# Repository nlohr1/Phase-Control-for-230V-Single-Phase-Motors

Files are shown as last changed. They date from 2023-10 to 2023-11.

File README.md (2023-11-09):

### Readme-Content:
- [Basic Schematic](#phase-control-for-230v-single-phase-motors-v2)
- [Module-Alignments](#alignment-v2-of-used-modules-on-a-5mm-acrylic-base-board)
- [Main-Schematic](#main-schematic--wiring-connections)
- [Safety-features](#safety-features)
- [Disclaimer](#readme-contents)
- [Principle-description](#principle-description)
- [The Wiring Board](#the-wiring-board)
- [Speedometer](#speedometer)
- [Schematic and Layout of the DIY-Speedometer](#diy-speedometer)
- [DIY-Boards + PCB-Layout](#diy-boards)

# Phase-Control-for-230V-Single-Phase-Motors
### Corrections and small modifications on new version Main_v2:  
- Another alignment purpose, which saves space.  
- The Emergency-Switch now is placed correctly within the "Off"-Switch wiring-line. Previoulsy it was wrongly placed within "On"-Switch line.  
- A second, passive 220k&Omega;2W-Resistor is placed after the Reversing-Switch between the two Motor-Supply-Lines (U1 and U2), instead on the wiring-board, to ensure save voltage-unload of the Motor-"Fire" EMI-Filter.

**⇒ &nbsp;New files in v2:**  
&#45; Main_v2 (base-folder for v2)  
&#45; Wiring-Board-Nano_v2 (sub-folder)  

This is a Control-Board for direction-switchable 230V *direct current* (DC)-motors, whose speed (rpm) can be controlled using a Potentiometer *or*  
using a PWM (Pulse Width Modulation) Signal in the low voltage range, generated here by a microController (Arduino Nano).

&nbsp; &nbsp;*Phase-Control schematic: **Priciple for 230V DC-Motors** with reversing-switch.*  
325V-DC-Motor-on-Phase-Control_Principle-Diagram

The picture above shows a basic diagram for the electronic control of a 230V **DC** motor, e.g. a hobby lathe, connected to a **single-phase** (230V) **AC**-current network.

Phase control circuits are often used for simple speed controls, here with an additional Bridge-Rectifier for 230V DC electric motors,
which are often used in medium power hobby machines (up to 10 amps ≙ approx. 2300 watts), such as lathes, milling benches, etc.

### Alignment-v2 of used modules on a 5mm acrylic base-board:
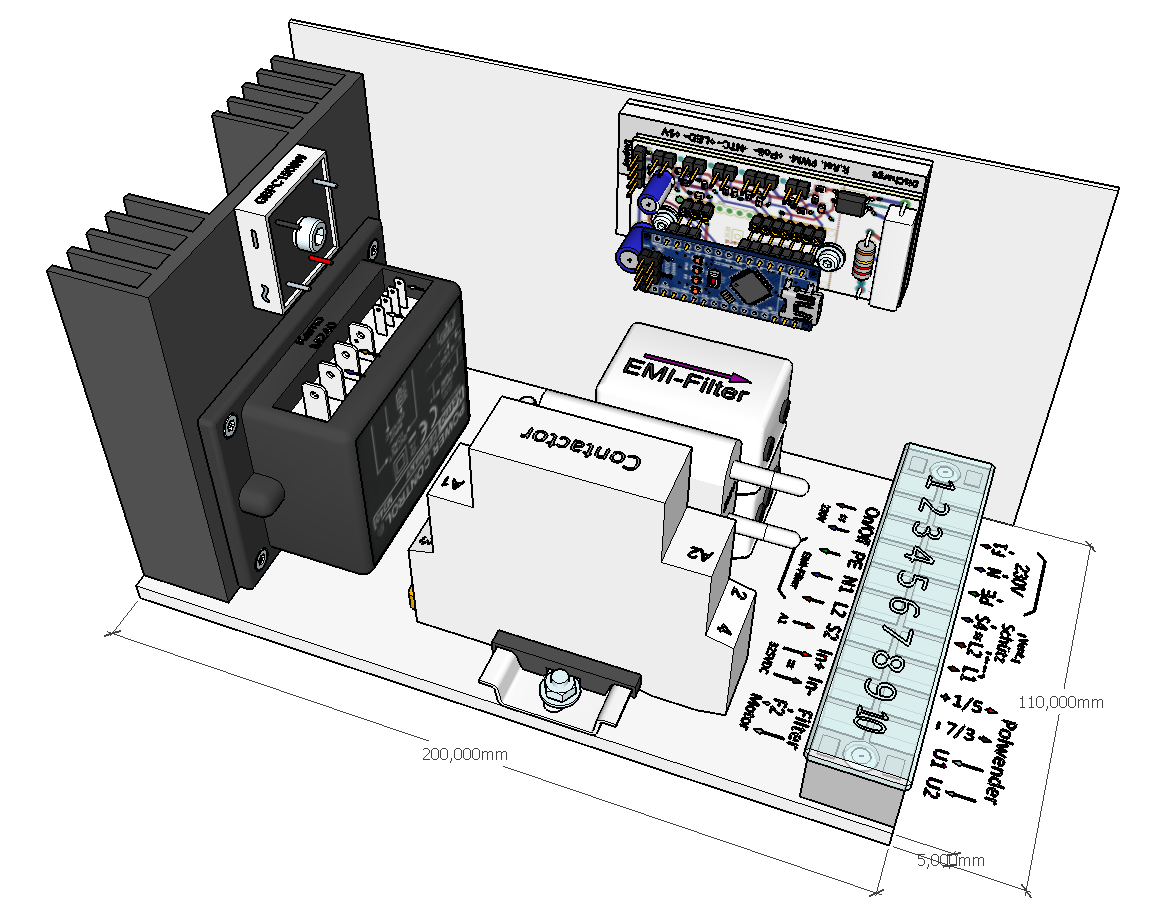
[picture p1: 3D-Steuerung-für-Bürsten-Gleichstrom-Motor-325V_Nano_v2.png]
3D-Steuerung-für-Bürsten-Gleichstrom-Motor-325V_Nano_v2
  
Since electronic controls of 230V *DC* motors in today's hobby machines (such as lathes, milling benches, etc.) often are built with
inexpensive components that are not really protected against surges or current peaks – some electronic-failures are inevitable.
So I decided to use a circuit that works a little more reliable, with electronic components and *modules* that are readily available
on the market *and* at the same time are better protected against voltage-glitches, overloads, incorrect operations and engine over-temperature.
All 230VDC (Direct Current!) brushed motors with up-to 2300 Watts can be controlled with this phase control board. It allows to control
the speed of the motor (0-100%) as well as the motor direction of rotation.

### Main Schematic / Wiring Connections:
⇒ *(the DIY-Wiring-Board with the Ardujino-nano here is yellow-framed)*
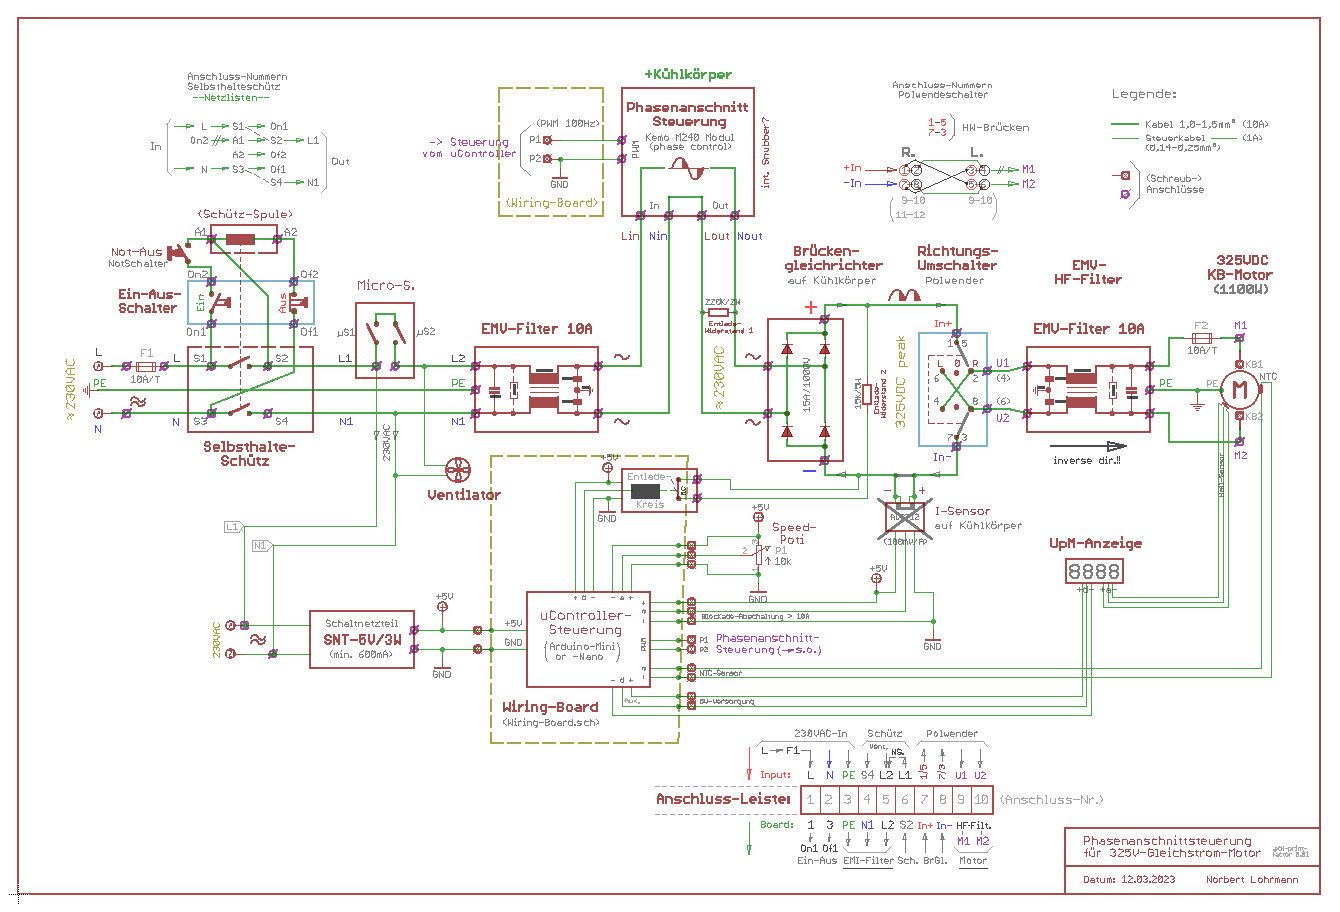
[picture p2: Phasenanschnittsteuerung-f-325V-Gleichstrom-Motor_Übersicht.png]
Phasenanschnittsteuerung-f-325V-Gleichstrom-Motor_Übersicht_DE


## Safety features
This circuit has some essential safety-functions:
- The main module "Kemo-M240" used here contains an integrated soft start, needed to start up strong motors (>800 - 2300 Watts),
   to avoid the tripping of standard 16A household fuses
- This main-module also contains an automatic overload or anti-lock shutdown with electronic reset
- If the used Motor contains a built-in NTC-thermistor (with 100kOhm), the µController can provide a protection against
   engine overheatings: if the motor-temperature exceeds 80°C, the µC goes into an endless loop, and reactivating PWM
   is only possible by switching off (main-power) or by pushing the reset-button of the µC.

!!!: Protection against direction of rotation switching ***while driving*** is **NOT** provided: if so an "EMF short circuit" occurs,
the "Kemo-M240" controller shots the power-control off in a fractions of a second and thus at least the mechanics of the machine is protected.
Electronics then can only be reactivated after a complete restart - either per µContoller-Reset or after a complete Main-Power Shutdown.

## Disclaimer:  
!!! It goes without saying that you reproduce this circuit at your own risk and responsibility !!!
Anyone who does not have sufficient knowledge of how to handle *dangerous* 230VAC currents or 325VDC(ss) voltages(!):
If you are not familiar with electrical or electronic components, you should either hire a specialist to do it for you
or stay away from it!
“Experiments” without special knowledge and appropriate protection(s) on high voltages can quickly end in death
following an electric shock! And sudden cardiac-arrest can occur even days after an electric shock! - if then
no immediate help is nearby...
In any case, a replica of this project is done expressly and explicitly *at your own risk*!

**Further notes:**
- Three-phase motor control is excluded due to the principle! This circuit only controls single phase Engines!
- The circuit also works with (simpler) *AC* single-phase asynchronous motors - omitting the bridge rectifier used here.
   However, a connected ***AC*** motor then is no longer direction-reversible.
- It is NOT suitable for capacitor motors! - "Capacitor starting motors" are often only used for simple purposes and
   built+used for on/off operation only (such as for smaller hobby drill press machines) - and are not speed-regulated.
   But it depends specifically on the type of engine, some capacitor motors can still be regulated (speed-limited).
   However, any weak to poor efficiency that so occurs should be taken into account (including heat losses).

Factual suggestions for improvements and changes are always welcome!

## Principle description:
The control works according to the 230VAC phase control principle (similar to a lamp dimmer), but in contrast to this
it can neutralize EMF (electromotive forces) of greater motors and is determined by special selection of used electronic components.

The Kemo-240 control-module is controlled via PWM (Pulse Width Modulation). This (low-voltage: 5VDC) PWM-signal is generated
with a “Arduino-Nano” micro-controller and (if present), this µC also evaluates an NTC-Sensor installed within the Motor, to check
a possible motor-overtemperature.
The Speedometer (RPM display on a LED display) does not run - as usually *independently* of the main phase-control, 
but sends back a "busy" signal to the µController, which therefore "knows" when the motor is running or not
(=when it is standing still), in order to ensure active discharge of the triac snubber and the EMI or EMC-filters charged
through supplied voltages + motor back EMF, to avoid uncontrolled jerky startings of the DC-motor after changing the direction of rotation.

The control consists of several modules chained(wired) one behind the other:

1. the 10AT fuse (F1) and the on/off switch with the self-holding latching contactor,
2. the (mandatory) safety switches plus other 230V safety microswitches on the specific machine,
3. the upstream EMC filter (= ElectroMagnetic Compatibility), here called EMI filter (serves to avoid incoming E.M. interferences),
4. the actual (triac) phase control, using *either* a potentiometer *or* a µController with PWM-output (Pulse-Width Modulation),
5. in parallel the 5V low-voltage circuit with the "Arduino-Nano" module, to generate the PWM for the phase control (2nd. version), 
   with additional, software-side monitoring of eventual motor-over-temperature,
6. the 15A/1500V bridge rectifier,
7. the reversing switch, also called “pole inverter” or direction of rotation switch,
8. a second EMI (carbon-brush-"fire"-) suppression filter + a second 10AT motor fuse (F2), and
9. at last the 325V DC (=direct current) motor.

230v-Wiring between modules and the outside-parts (rear 230V inlet-panel, front machine-control-panel, motor-connections) have to be connected safely
through PVC-isolated 1mm² wires (about AWG 17) and in-between through isolated threaded-connectors or clamping-connectors with 16A/230V.
I used lever clamps ("WAGO Hebelklemme 221-2411") for most of the "flying"-connections.  
For all 5Volt (=low-voltage) connections I used smaller wires (about 0.25-0.75mm² = AWG-23 upto AWG-20) with JST-Connectors (2-, 3- and 4-wired),
as connectors for the wiring-board. Of course also it's possible to use above mentionned WAGO-connectors for smaller wires.  
**Att: Reliability of connections** is VERY IMPORTANT, so dont choose cheap (=mostly bad) connectors, due to 99% of all electical problems
are resulting from loose contacts/connections!

## The Wiring Board:
The two DIY-parts in this chain that still needs to be soldered together + programmed are the “wiring board” and the DIY-Speedometer.  
The Wiring-board serves to wire/connect the Low-Voltage PWM-Signal to the main phase control module "Kemo-M240" and to other low-voltage connections
as the Panel-Signal-"On"-LED, the NTC-Sensor and the 10k&Omega;-Poti.  
This wiring board also contains the Arduino Nano µController as the heart of the circuit, some passive components (resistors + capacitors) and above mentionned
(JST-)Connectors plus a 4-wire JST-Connector for the Speedometer (rpm display) and the 230VAC Discharge Circuit (Power-Resistor), this to avoid uncontrolled,
jerk startings of the motor while switching it into reverse-direction.
Wiring-Board-Nano_sch
*Circuit diagram of the low-voltage circuit "wiring board" with the Arduino Nano*  
Wiring-Board-Nano_3D

This wiring board with the Arduino Nano is provided as schematic and as PCB-layout in Eagle format - which can easily be converted
into other formats. Included are also .pdf-files and layouts, prepared for the DIY "toner-direct-method" and for external PCB-Services.

## Speedometer:
Speedometer

## DIY-Speedometer:
4x7-Segment-LED-Display-Module

**Schematic and Layout of the DIY-Speedometer**:  
Tachometer-with-4x7-Segm-LED-Display_sch
Tachometer-with-4x7-Segm-LED-Display_pcb

The DIY-Speedometer consists of a 4-digit LED-display-module and a "Arduino Mini Pro"-module (inside the case) with 2 pieces of 10k resistors to GND.  
This tachometer can either be “manually wired”:
- by wire-connecting a 4-digit LED-Display module to a (Arduino-)Mini-Pro board + 2x 10k resistors to GND,
   or
- soldering SMD-parts on a DIY-Board with above provided layout. For this purpose I included Schematic + Layout, as well as BOM (Bill of Materials).

A speedometer to display the speed of the motor can also be purchased as a (ready-made) module - but this modules have no "running" monitor Signal and
so the discharge-unit (on the wiring-board) is no longer switching on/off (as needed for the 15k-Resistor R9).

## DIY-Boards:
Anyone who is familiar with DIY-etching of circuit boards can either use the 2-sided Toner Direct Method (see .pdf plans for 2-sided copy in 1:1 scale) or
give-it-out to an external PCB layout-service.  
In a further -separate- article I will describe a new and simpler method to make exact 2-sided DIY-PCB-layouts through laser-burning "resting"
ink-protect areas on the PCB-board (resting "black" areas: substracted isolated wiring-lines from the total surface).

All Documents are available as Eagle layouts, png-Image-Files and pdf-Files and also as Gerber+Excellon files (attached CAM .zip archives).  
So also both Arduino Sketches (for the Arduino-Nano "heart"-Module: "Firmware-Nano.ino" and the Sketch for the **DIY**-Speedometer-*Board* including a "naked"
ATmega328-µController + 4x7-LED-Display ***or*** for the wired version with an Ardino-Mini-Pro-*Module* + 4x7-LED-Display(-module).  
Both variants of the DIY-Speedometer are using the "Tachometer-using-Arduino.ino" sketch.  

Thereto I've enclosed also a 3D-printable case + frame-parts for the Tachometer, adapted to insert+glue the 4x7-LED-Display module.
-----

Github-Link: [https://github.com/nlohr1/Phase-Control-for-230V-Single-Phase-Motors](https://github.com/nlohr1/Phase-Control-for-230V-Single-Phase-Motors/blob/main/README.md)

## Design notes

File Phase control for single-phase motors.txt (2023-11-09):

Phase control for single-phase motors - up to 2300 watts
--------------------------------------------------------

Control for direction-switchable 230V *direct current* motors, whose speed (rpm) can be controlled using a
10k potentiometer *or* a PWM (pulse width modulation in the low voltage range) can be controlled via uController.

Priciple of a Poti-Controlled Phase-Control of 230AC/320VDC Motor
(3D image of the entire motor control)

Phase control circuits are often used for speed control, here a PA with a downstream one
Rectifier for reversible 230V DC electric motors, which are often used in hobby machines
medium power (up to 10 amps or up to approx. 2300 watts) such as lathes and milling benches.

Since the electronic controls of 230V *DC* motors in today's hobby machines such as lathes, milling benches, etc.
often have inexpensive components that are not protected against surges or current peaks – therefore
unfortunately failures are inevitable, so I decided to use a circuit that works a little more reliable,
with electronic components and *modules* that are readily available on the market and more reliable.
All 230VDC (direct current!) carbon brush motors with up to 2300W can be controlled with this phase control.
It allows you to control the speed of the motor (0-100%) as well as the motor direction of rotation.

Safety features of this single-phase speed-control:

In addition, this circuit has essential safety circuits:
- The main module "Kemo-M240" used here contains an integrated soft start, needed to start up larger motors,
   to avoid the tripping of standard 16A household fuses
- This module also contains an automatic overload or anti-lock shutdown with electronic reset
- If the motor contains a built-in NTC thermistor (with 100kOhm), the µController can provide a possible
   Monitor engine overheating protection. When 80°C is exceeded, the µC switches off the PWM goes into an endless loop,
   and can then only be reactivated by switching off the power or by pushing the reset-button of the controller.

!!!: Protection against direction of rotation switching *while driving* is NOT provided here: Due to this, if
an "EMF short circuit" occurs, the "Kemo-M240" controller switches off very quickly and thus at least protects
the mechanics of the machine. The electronics can then only be used again after a complete restart or Power shutdown.

Disclaimer:
!!! It goes without saying that you reproduce this circuit at your own risk and responsibility!!!
Anyone who does not have sufficient knowledge of how to handle *dangerous* 230VAC currents or 325VDC(ss) voltages(!):
If you are not familiar with electrical or electronic components, you should either hire a specialist to do it for you
or stay away from it!
“Experiments” without special knowledge and appropriate protection(s) on high voltages can quickly end in death
following an electric shock! And sudden cardiac-arrest can occur even days after an electric shock! - if then
no immediate help is nearby...
In any case, a replica of this project is done expressly and explicitly *at your own risk*!

Further notes:
- Three-phase motor activations are hereby excluded due to the principle! This circuit only controls single phase Engines!
- The circuit also works with (simpler) *AC* single-phase asynchronous motors - omitting the bridge rectifier used here.
   However, a connected *AC* motor then is no longer direction-reversible.
- It is NOT suitable for capacitor motors! - "Capacitor starting motors" are often only used for simple purposes and
   built + used for on/off operation only (such as for smaller hobby drill presses) - and are not speed-regulated. But
   it depends specifically on the type of engine, some capacitor motors can still be regulated (speed-limited).
   However, any weak to poor efficiency that occurs should be taken into account (including heat losses).

Factual suggestions for improvements and changes are always welcome!

(principle sketch)

The picture shows a possible, basic structure or the basic diagram of the electronic control
DC motor, e.g. a hobby lathe, which is connected to a single-phase 230VAC alternating current network - therefore
This circuit is only designed for a maximum output of 2300 watt motors (=> 10A fuse!) - but what
should be sufficient for most machines in the hobby sector (⇒ pay attention to the motor nameplate!).

(Main Wiring Diagram)

Principle description:
The control works according to the 230VAC phase control principle (similar to a lamp dimmer), but in contrast
it may neutralize the EMF (electromotive force) of a motor and is determined by the selection of electronic components.
A higher quality module is used to control the motor, which is controlled via PWM (Pulse Width Modulation).
The micro-controller “Arduino-Nano” used here generates the PWM and (if present) it also evaluates an NTC sensor
installed in the motor, to check any possible Engine overtemperature.
The speedometer for speed display does not run - as usually - *independently* of the main control (RPM display on a LED display), 
but also sends back a "busy" signal to the µController, which therefore "knows" when the motor is running or
when it is standing still, in order to ensure active discharge of the triac snubber and the EMI or EMC-filters charged
through supplied voltages and the motor back EMF, in order to avoid an uncontrolled, jerky starting of the DC-motor
after changing direction!

The control consists of several modules “wired” one behind the other:

1. the 10AT fuse and the on/off switch with latching contactor,
2. the (mandatory) safety switches or other 230V safety microswitches on a specific machine,
3. the upstream EMC filter (= electromagnetic compatibility), here called EMI filter (to avoid E.M. interferences),
4. the actual PWM (triac) phase control (control using a potentiometer *or* pulse-width modulation),
5. in parallel the low-voltage electronics (+5V/GND) to generate the PWM for the phase control, using an "Arduino-Nano"
    module with additional software-side monitoring of eventual motor-over-temperature with external NTC-sensor,
6. the 15A/1500V bridge rectifier,
7. the “pole inverter”, also called reversing switch or direction of rotation switch,
8. a second EMI (carbon brush fire) suppression filter + a second 10AT motor fuse,
9. and at last the 325V DC (=direct current) motor.

The only part that still needs to be soldered together + programmed is the “wiring board” to connect the Low-Voltage
PWM-Signal to the main phase control module "Kemo-M240". This wiring board contains also the Arduino Nano µController 
as the heart of the circuit, some passive components (resistors + capacitors) and the JST-Connectors for Sensors
and the tachometer (rpm display) + the Discharge Circuit for both Discharge Resistors, to avoid uncontrolled
starting impulses / jerk starting of the motor switching it to reverse-direction.

The “wiring board”:
(Circuit diagram of the low-voltage circuit "wiring board" with the Arduino Nano)
(3D image of the "wiring board")

The “wiring board” with the Arduino Nano is provided as schematic and as PCB-layout in Eagle format - which can
easily be converted into other formats.

Speedometer:
(Picture)

The modified speedometer consists of a 4-digit LED display and an "Arduino Mini Pro" with 2 pieces of
10k resistors to GND. This tachometer can either be “manually wired”:
- by wire-connecting the 4-digit LED-Display to the Mini-Pro + 2x 10k resistors to GND,
   or
- soldered together on a SMD-Board with the provided layout. Both Schematic + Layout as well as the BOM
  (Bill of Materials) + Software are included.

The speedometer for speed display/control can also be purchased as a (ready-made) module - but then
the running monitoring + also the unloading unit is no longer thereby (and can then be ignored).

Anyone who is familiar with the DIY production of circuit boards can either use the Toner Direct
Method (.pdf plans for 2-sided copy in 1:1 scale) or roll it out to an external PCB layout-service.
Documents are available both as Eagle layouts and as Gerber/Excellon files (in the .zip archive) attached.

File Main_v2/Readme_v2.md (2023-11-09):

### Readme_v2 Content:
- [Another Module-Alignment purpose]()
- [Main-Schematic v2]()
- [Wiring Board v2]()

# Phase-Control-for-230V-Single-Phase-Motors v2
### Corrections and small modifications on v2:  
- Another alignment purpose, which saves space  
- The Emergency-Switch now is placed within the "On"-Switch wiring-line. Previoulsy it was wrongly placed within "Off"-Switch line.  
- A second, passive 220k&Omega-Resistor is placed after the Reversing-Switch between the two Motor-Supply-Lines (U1 and U2), instead on the wiring-board, to ensure save voltage-unload of the Motor-"Fire" EMI-Filter.

**⇒ New files in in v2-folder:**  
&#45; this Readme_v2.md
&#45; Main_v2 (base-folder)
&#45; Wiring-Board-Nano_v2 (sub-folder)  

## Disclaimer:  
!!! It goes without saying that you reproduce this circuit at your own risk and responsibility !!!

### New Alignment of modules on the 5mm acrylic base-board in Base-board_v2:
![3D-Steuerung-für-Bürsten-Gleichstrom-Motor-325V_Nano_v2]()  

### Main Schematic_v2 / Wiring Connections:
⇒ *(the DIY-Wiring-Board with the Ardujino-nano here is yellow-framed)*
![Phasenanschnittsteuerung-f-325V-Gleichstrom-Motor_Übersicht_DE]()

## Wiring-Board_v2:
![Wiring-Board-Nano_v2]()
*Circuit diagram of the low-voltage circuit "wiring board" with the Arduino Nano*  
![Wiring-Board-Nano_3D_v2]()

<hr>

Github-Link: https://github.com/nlohr1/Phase-Control-for-230V-Single-Phase-Motors/

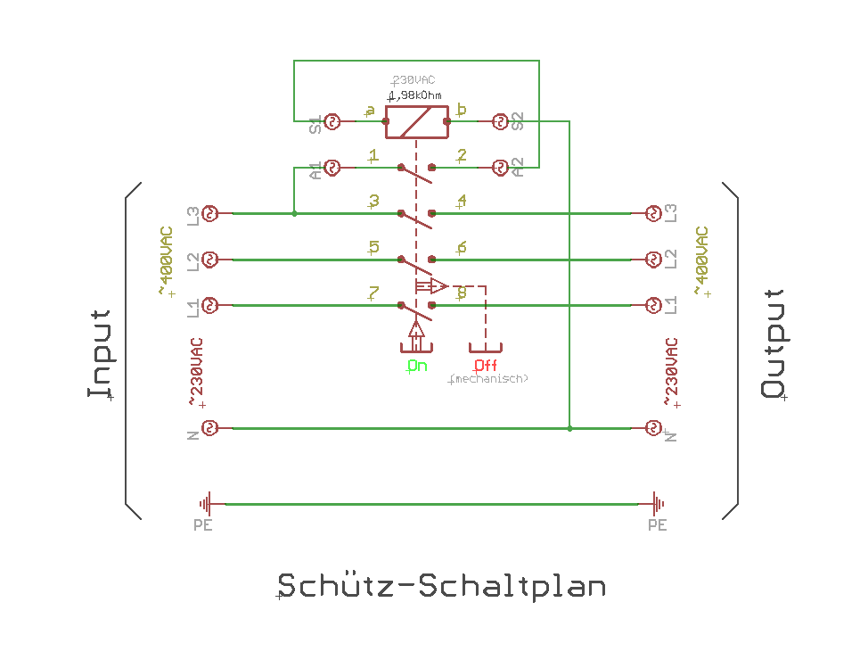
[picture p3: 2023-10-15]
DZ07B_EinAus-Schalter-mit-Schütz_Schaltplan-für-3-Phasen.png

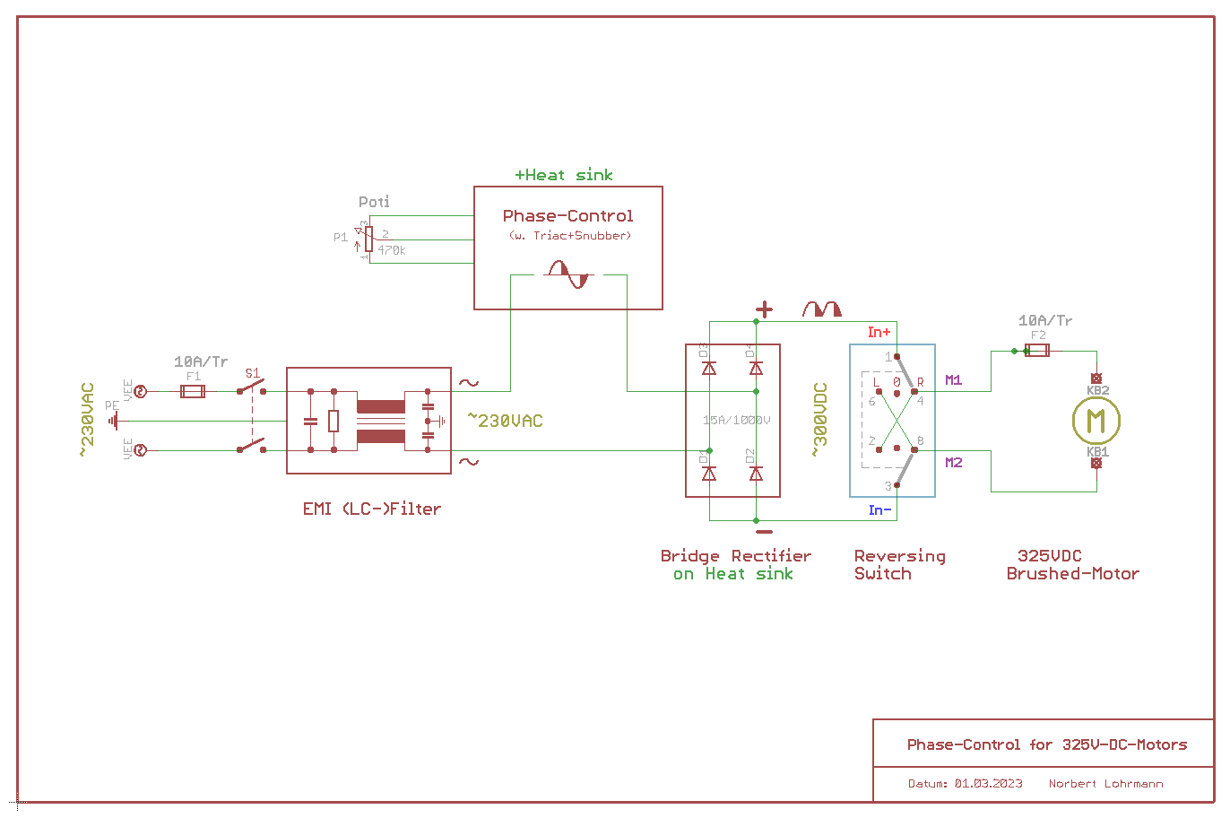
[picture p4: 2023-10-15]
325V-DC-Motor-on-Phase-Control_Principle-Diagram.png

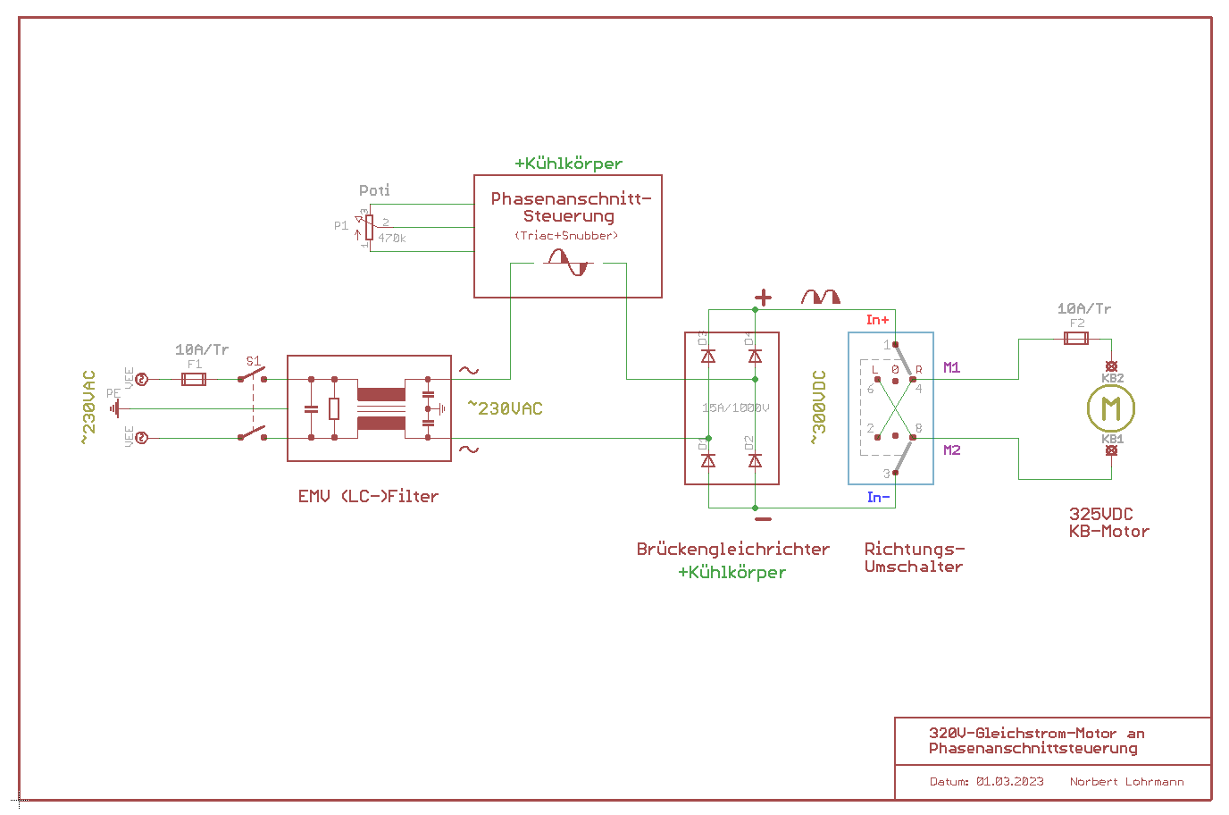
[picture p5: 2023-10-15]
325V-Gleichstrom-Motor-an-Phasenanschnittsteuerung_Prinzip-Schema.png

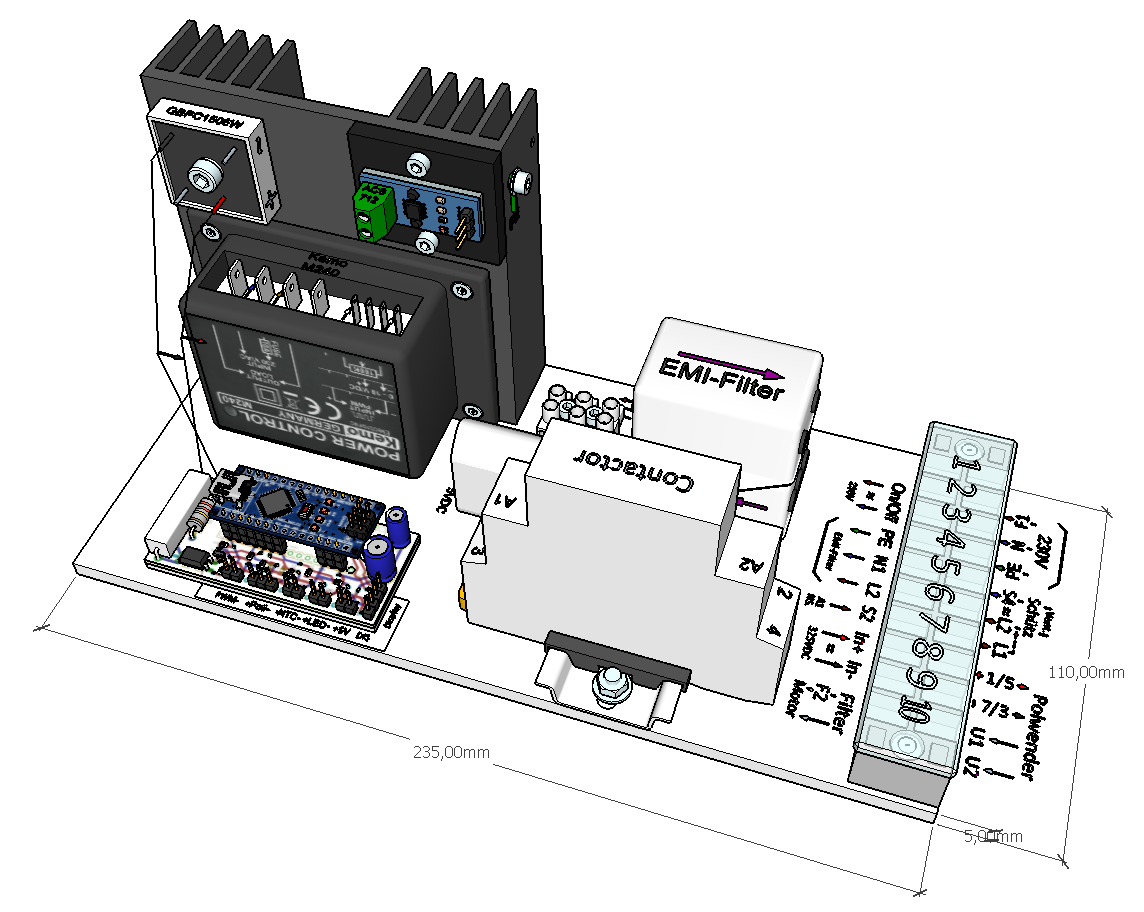
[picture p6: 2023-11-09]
3D-Steuerung-für-Bürsten-Gleichstrom-Motor-325V_Nano.png

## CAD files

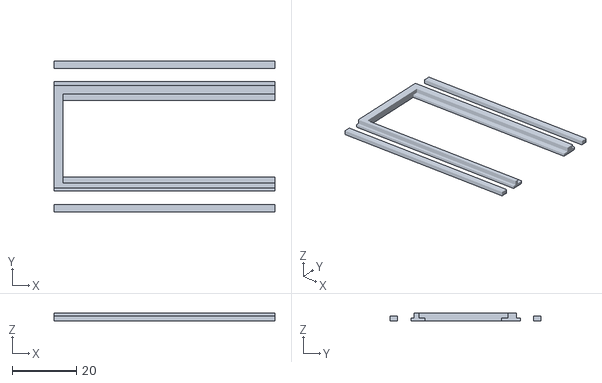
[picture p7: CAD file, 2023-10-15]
Tachometer_with_TM1637-IC_and_Arduino-Mini-Pro/Spacer-for-4x7-Segment-LED-Display-Frame.stl
69.0 x 47.2 x 2.50

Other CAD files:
Main_v2/Wiring-Board-Nano_v2/Wiring-Board-Nano_Bodenplatte.3mf
Main_v2/3D-Steuerung-f-Gleichstrom-Motor-325V_Lochung-der-Grundplatte_v2.skp
Main_v2/Wiring-Board-Nano_v2/Wiring-Board-Nano_3D_v2.skp
Main_v2/Wiring-Board-Nano_v2/Wiring-Board-Nano_Bodenplatte.stl
Tachometer_with_TM1637-IC_and_Arduino-Mini-Pro/4x7-Segment-LED-Display-Module.skp
Tachometer_with_TM1637-IC_and_Arduino-Mini-Pro/Spacer-for-4x7-Segment-LED-Display-Frame.skp
Wiring-Board-Nano/Wiring-Board-Nano_3D.skp

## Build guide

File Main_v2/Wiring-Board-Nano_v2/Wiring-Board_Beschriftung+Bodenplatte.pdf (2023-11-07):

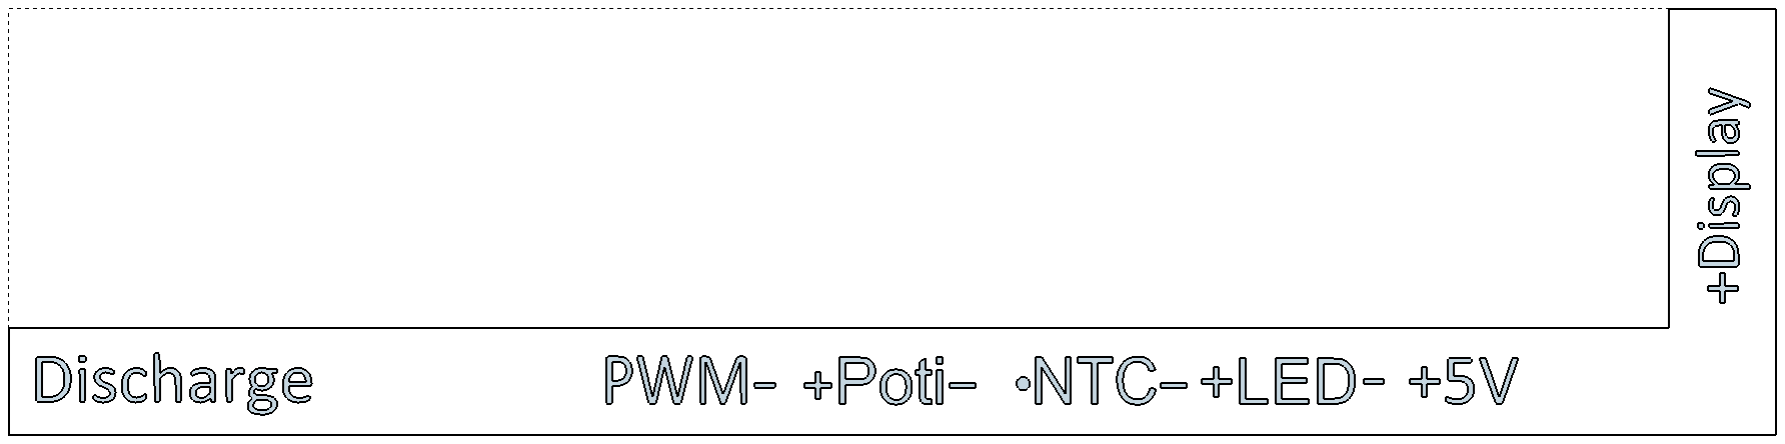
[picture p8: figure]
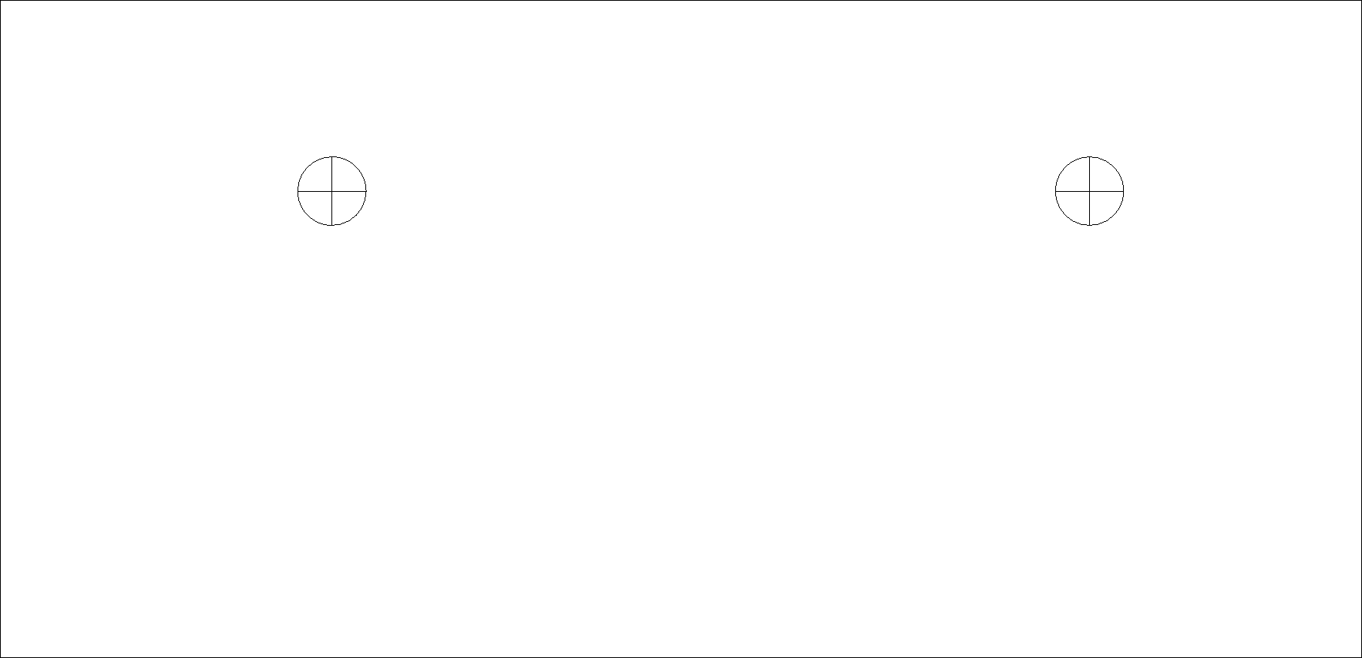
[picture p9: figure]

75,5 x 36,5 x #5 mm

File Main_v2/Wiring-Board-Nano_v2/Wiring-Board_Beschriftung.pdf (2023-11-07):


74,5 x 18 mm

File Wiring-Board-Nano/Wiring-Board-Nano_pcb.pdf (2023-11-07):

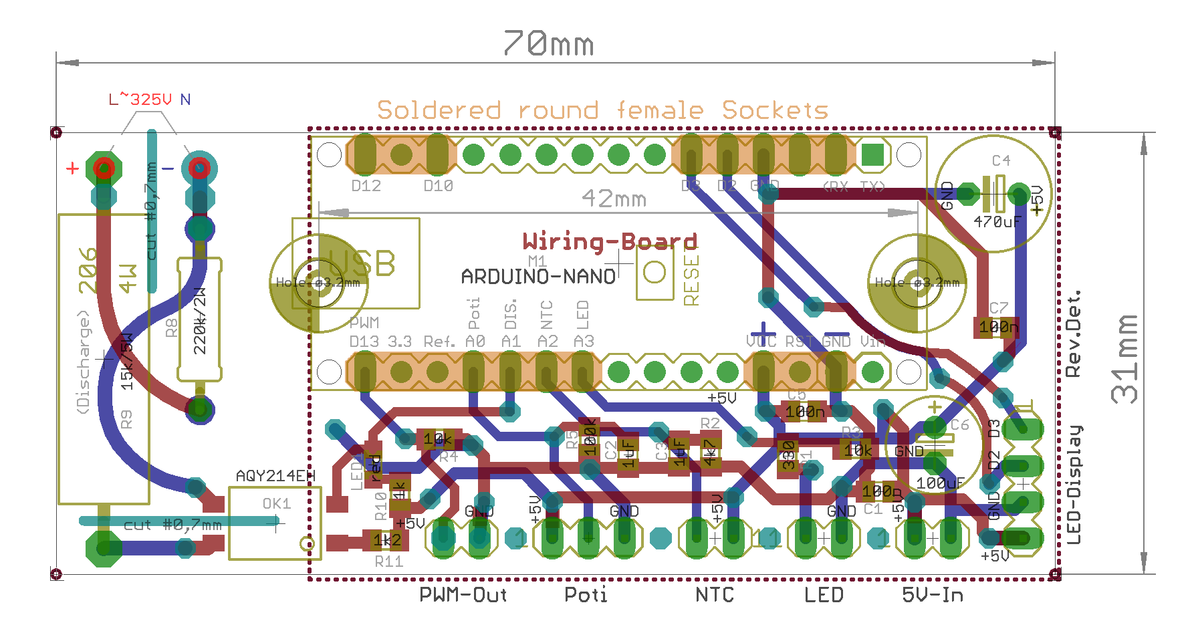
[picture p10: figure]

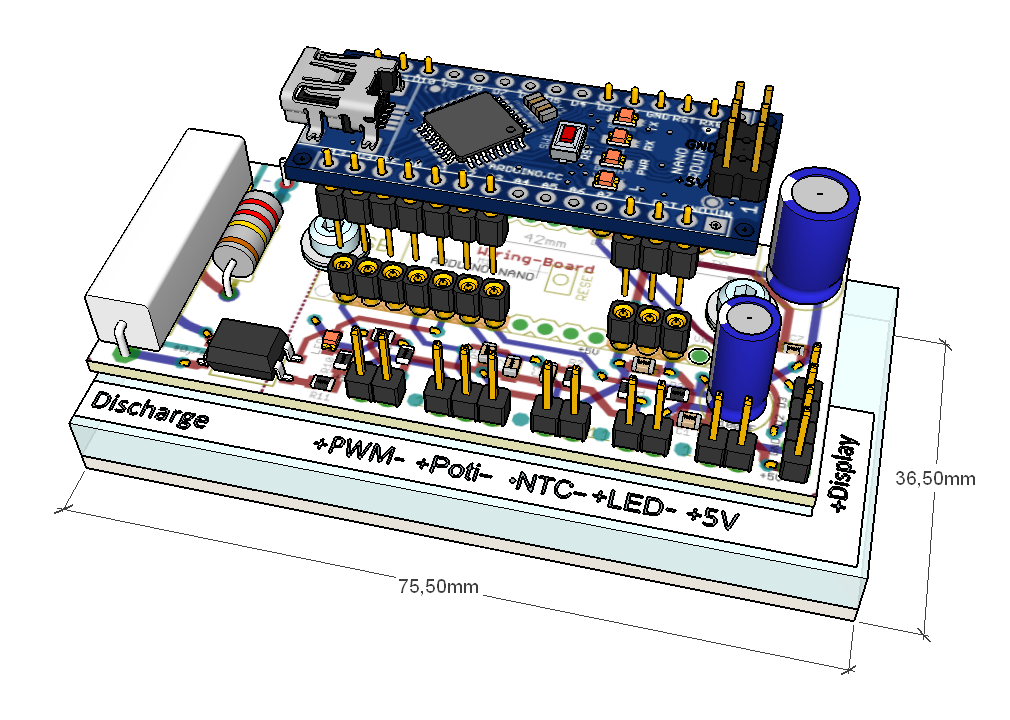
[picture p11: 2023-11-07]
Wiring-Board-Nano_3D.png

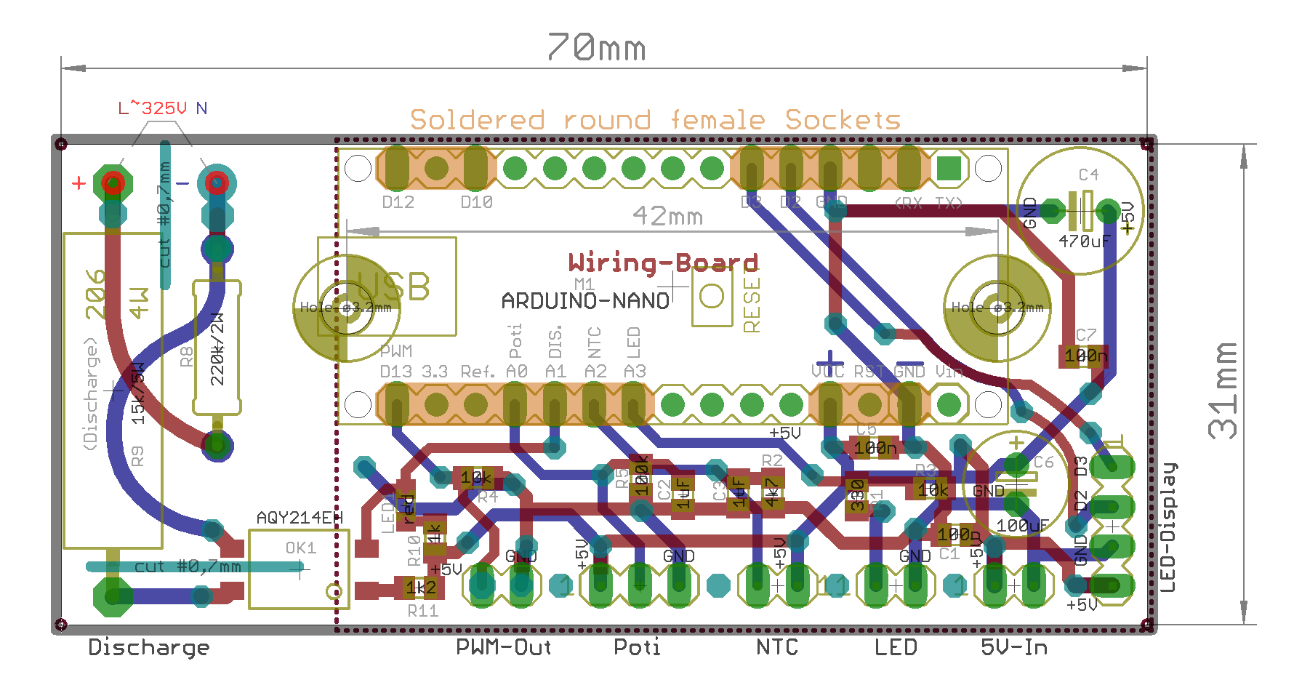
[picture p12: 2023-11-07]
Wiring-Board-Nano/Wiring-Board-Nano_pcb.png

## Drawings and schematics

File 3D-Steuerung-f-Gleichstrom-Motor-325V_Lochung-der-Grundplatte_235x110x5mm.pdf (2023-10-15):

## Acryl-Platte #5mm – 235 x 110 mm

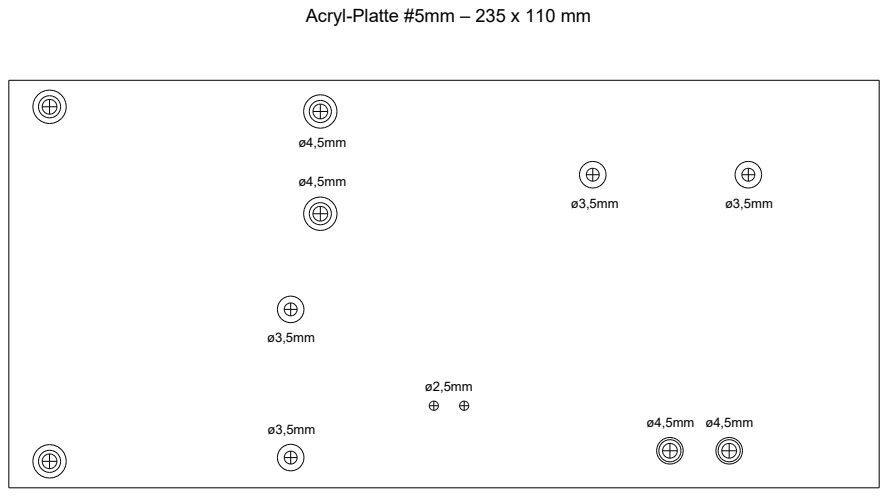
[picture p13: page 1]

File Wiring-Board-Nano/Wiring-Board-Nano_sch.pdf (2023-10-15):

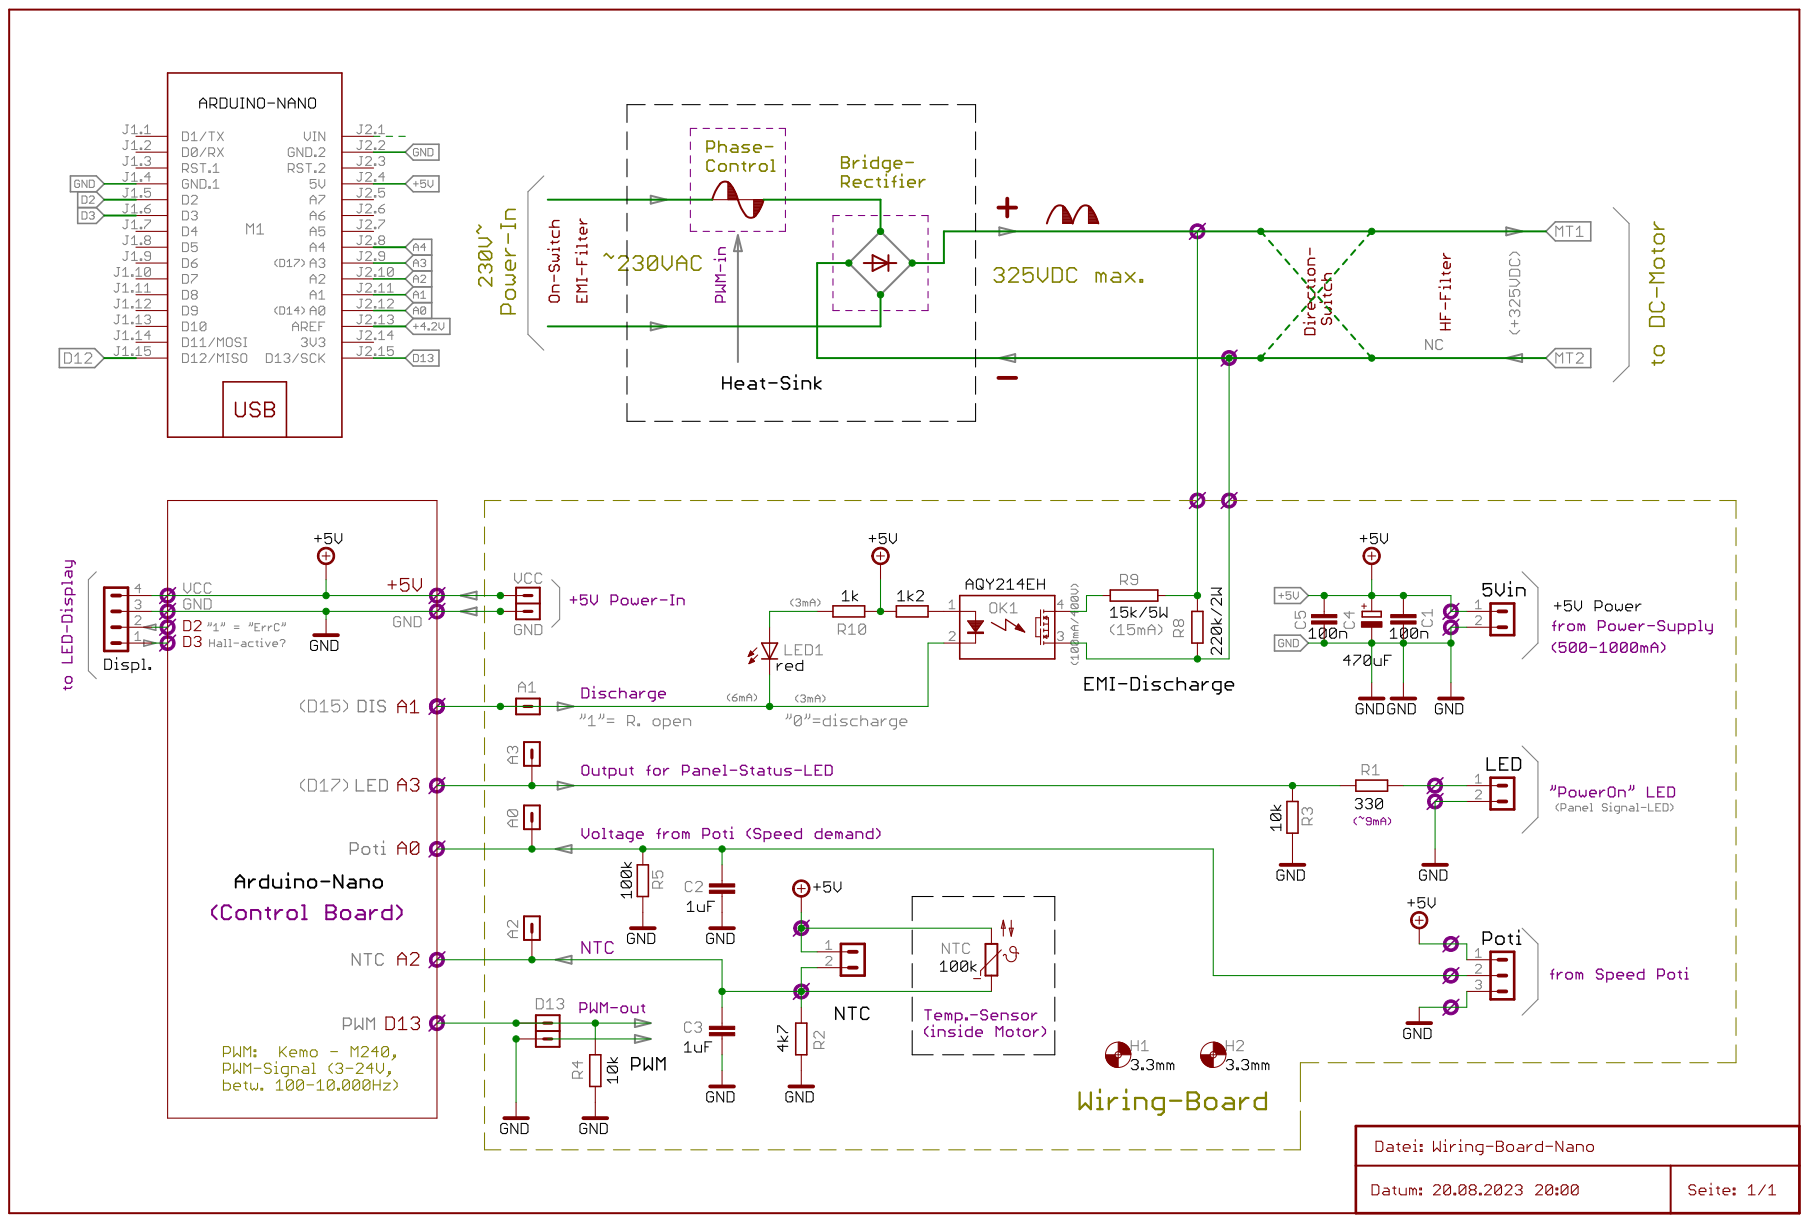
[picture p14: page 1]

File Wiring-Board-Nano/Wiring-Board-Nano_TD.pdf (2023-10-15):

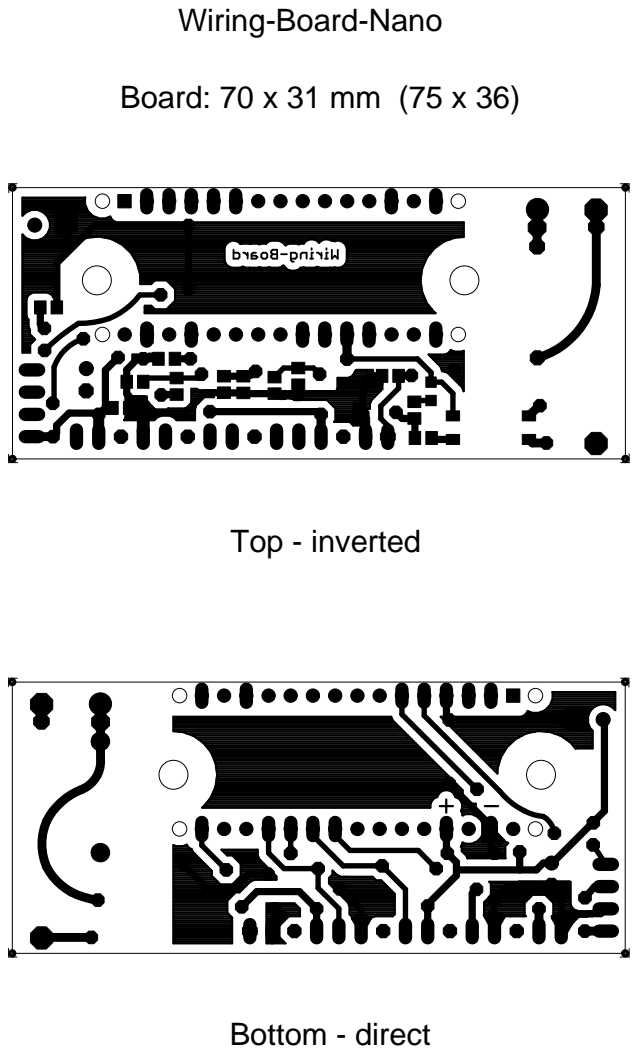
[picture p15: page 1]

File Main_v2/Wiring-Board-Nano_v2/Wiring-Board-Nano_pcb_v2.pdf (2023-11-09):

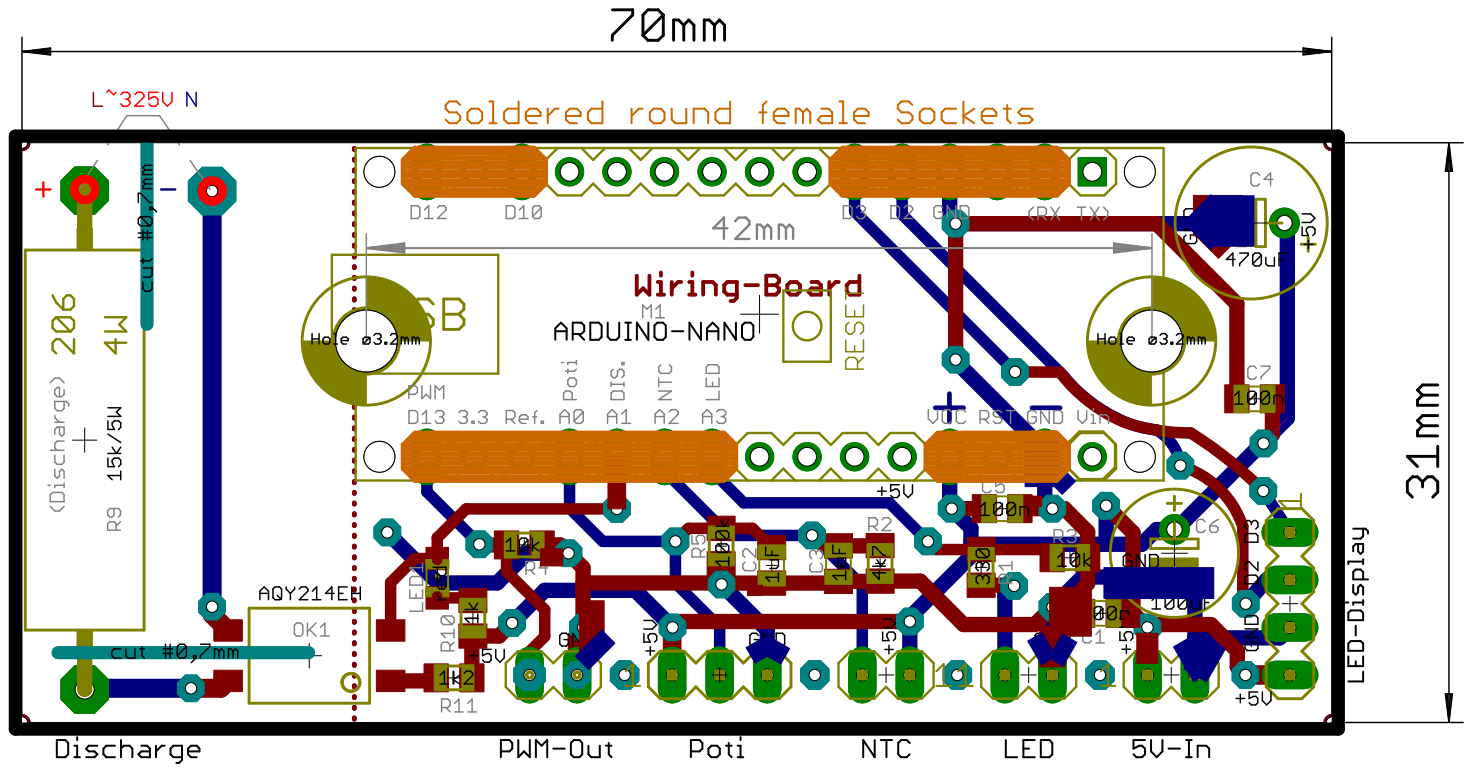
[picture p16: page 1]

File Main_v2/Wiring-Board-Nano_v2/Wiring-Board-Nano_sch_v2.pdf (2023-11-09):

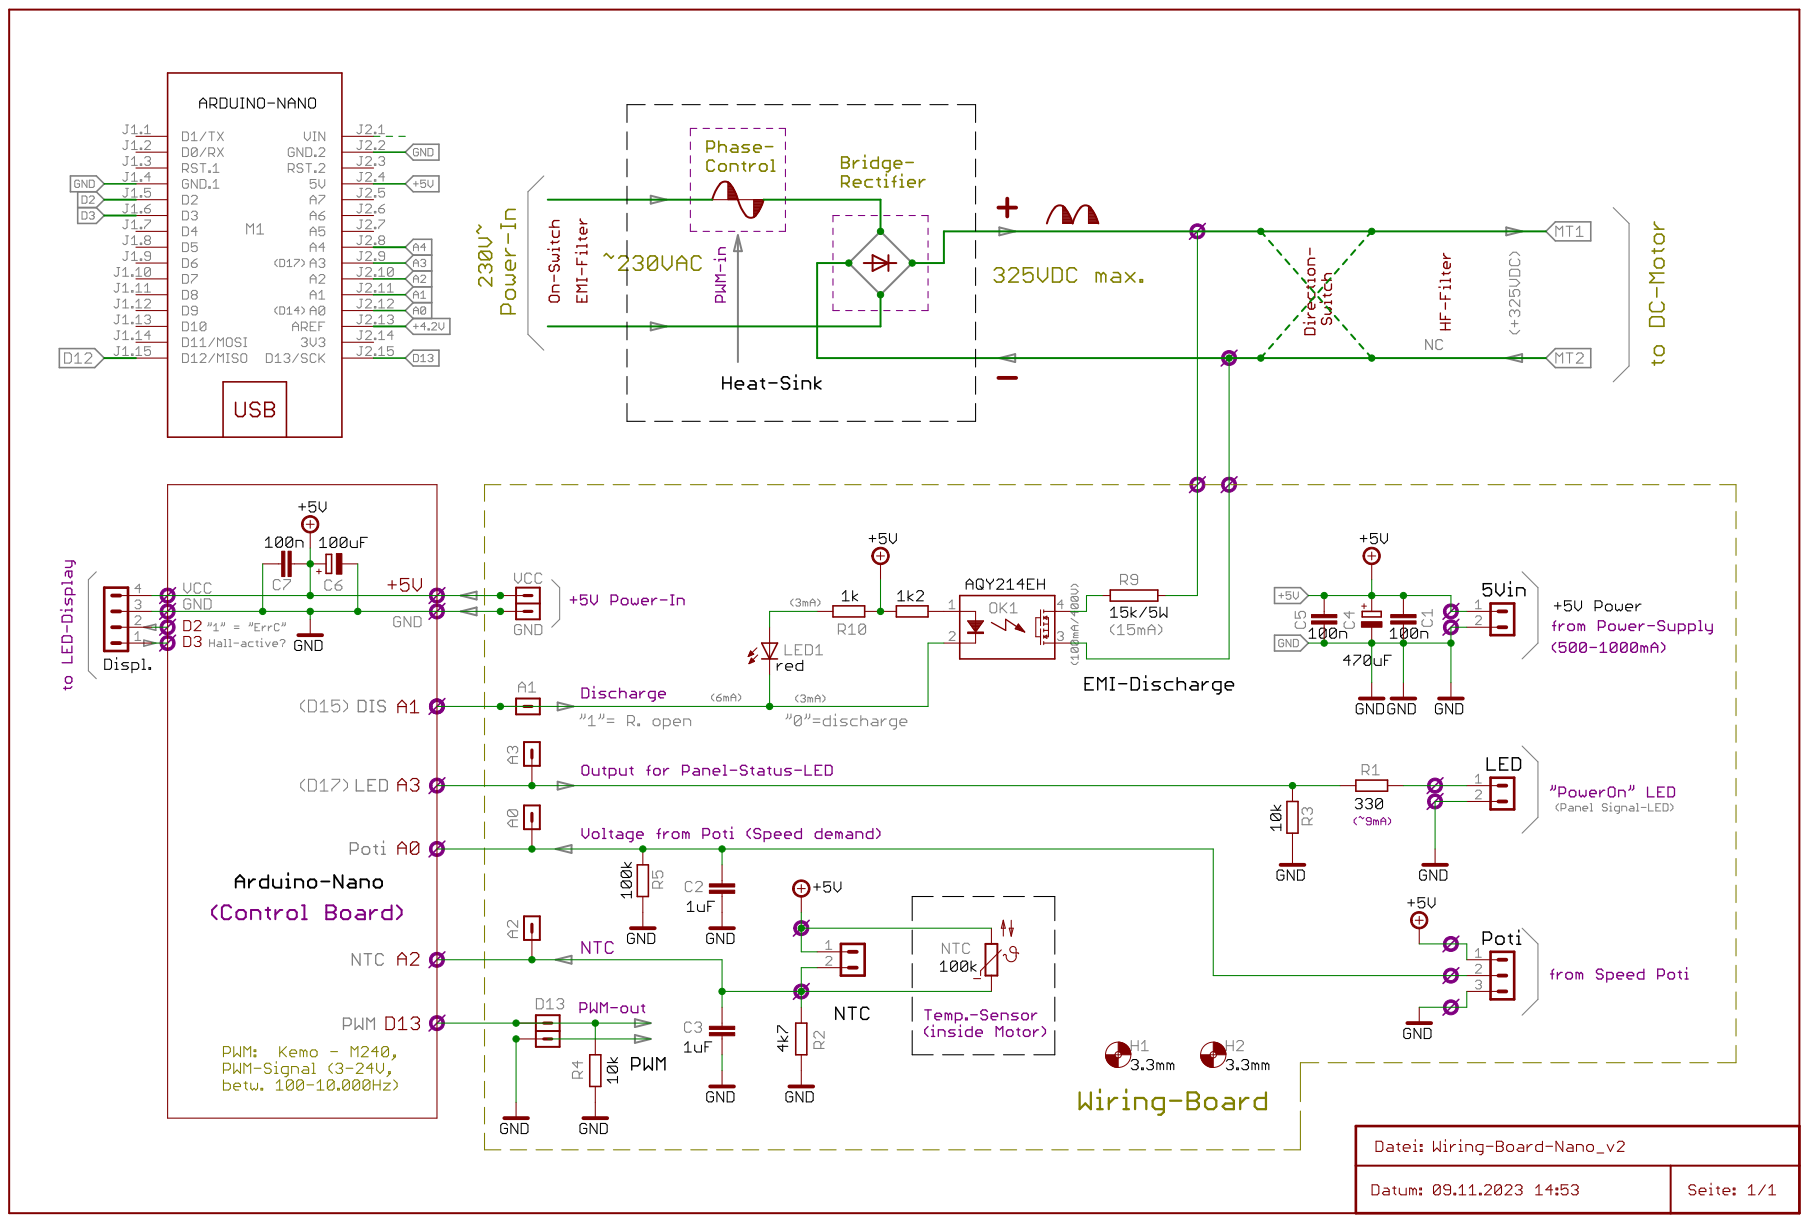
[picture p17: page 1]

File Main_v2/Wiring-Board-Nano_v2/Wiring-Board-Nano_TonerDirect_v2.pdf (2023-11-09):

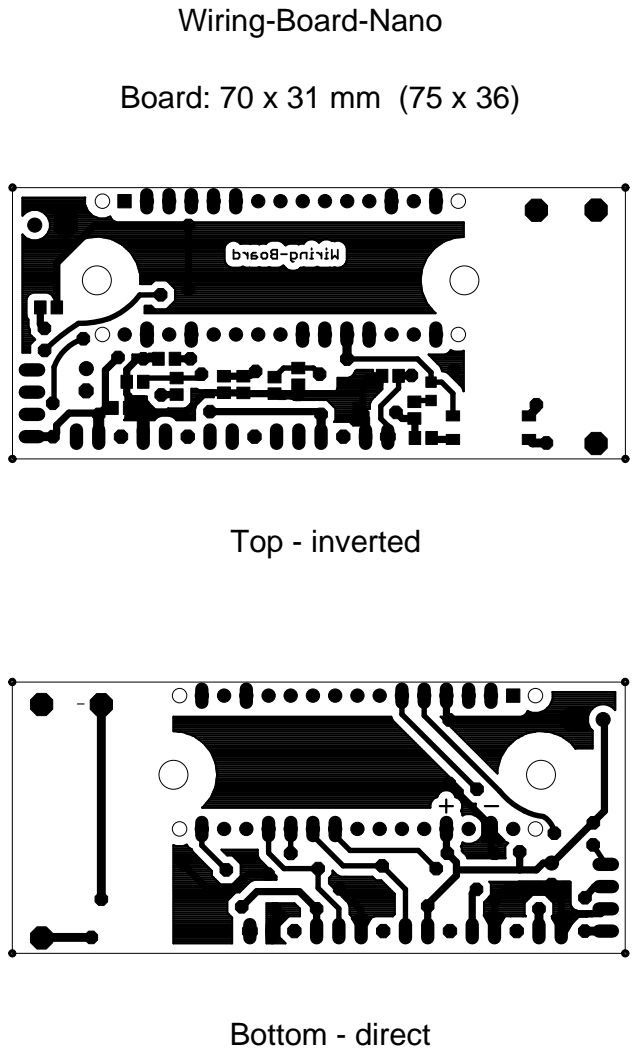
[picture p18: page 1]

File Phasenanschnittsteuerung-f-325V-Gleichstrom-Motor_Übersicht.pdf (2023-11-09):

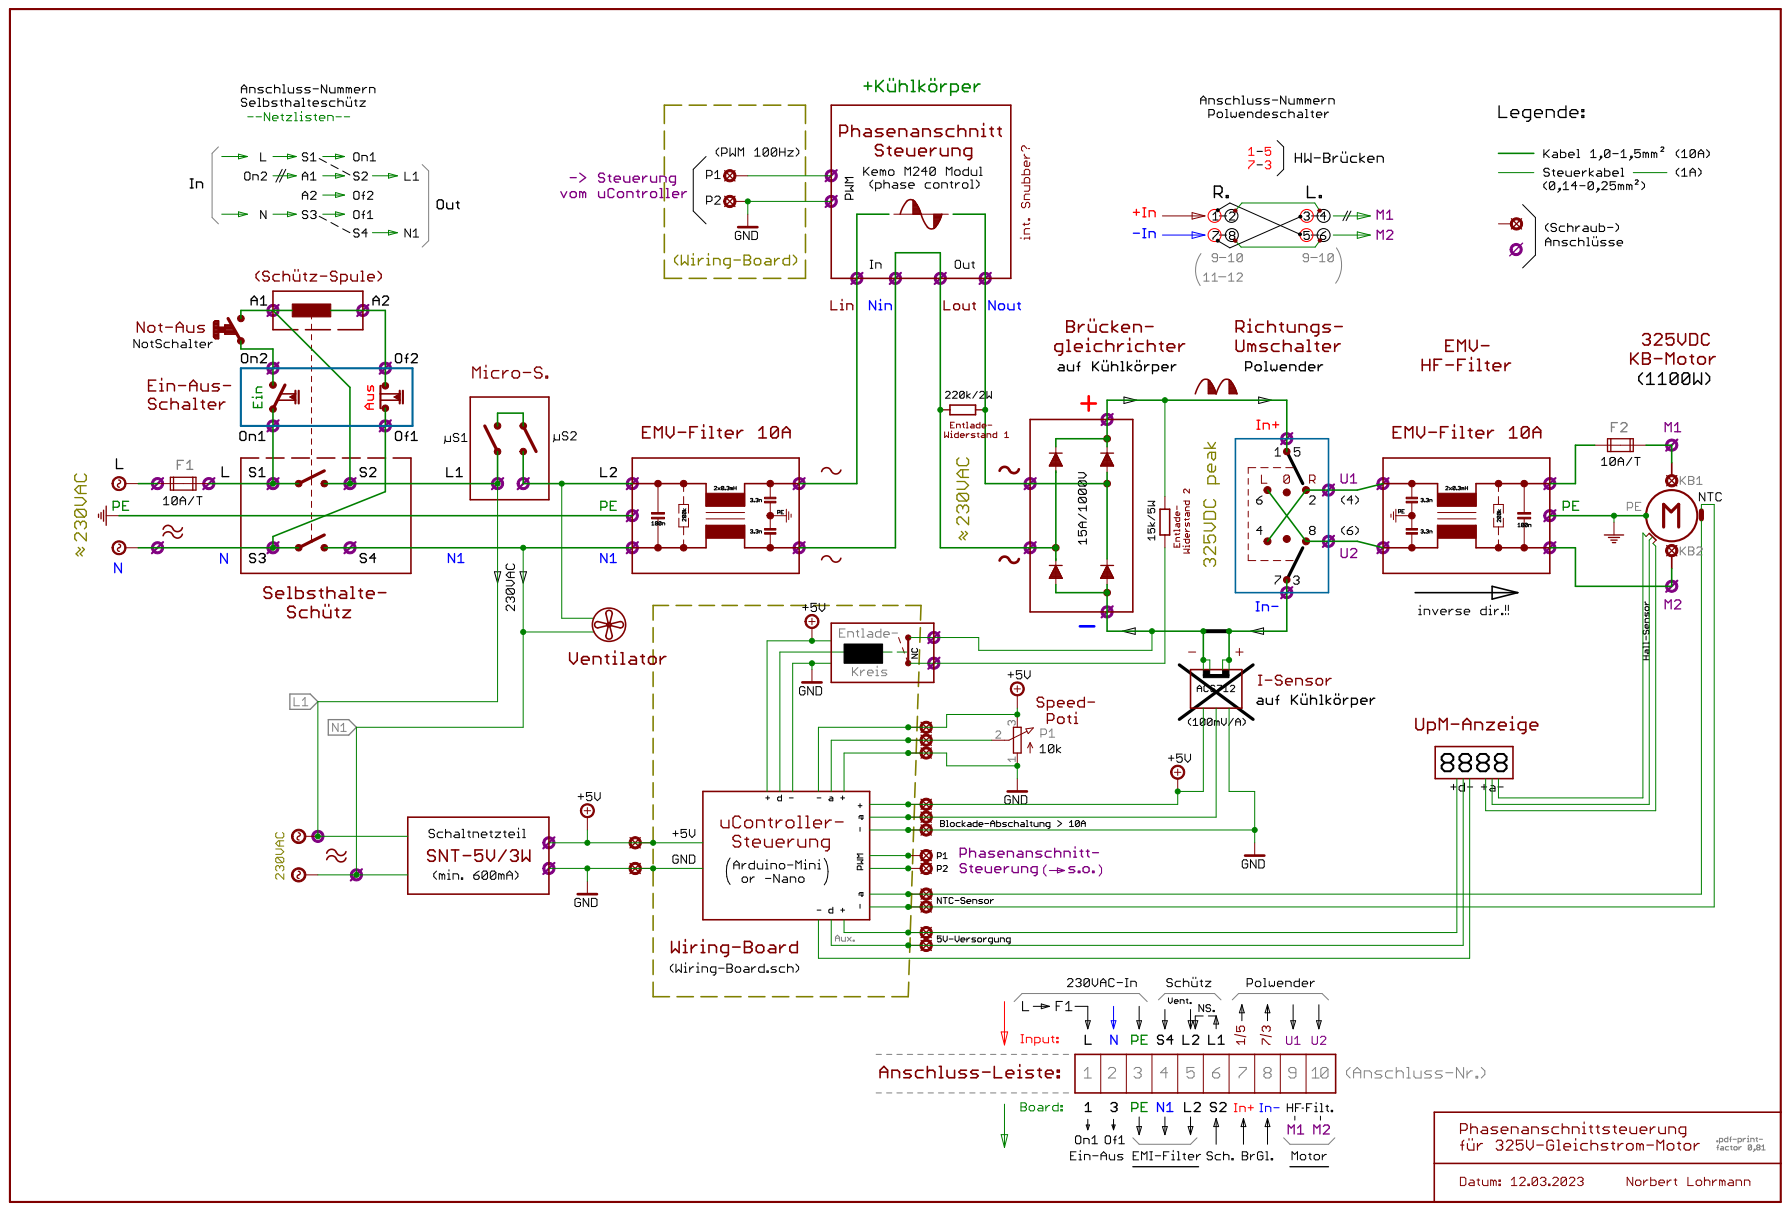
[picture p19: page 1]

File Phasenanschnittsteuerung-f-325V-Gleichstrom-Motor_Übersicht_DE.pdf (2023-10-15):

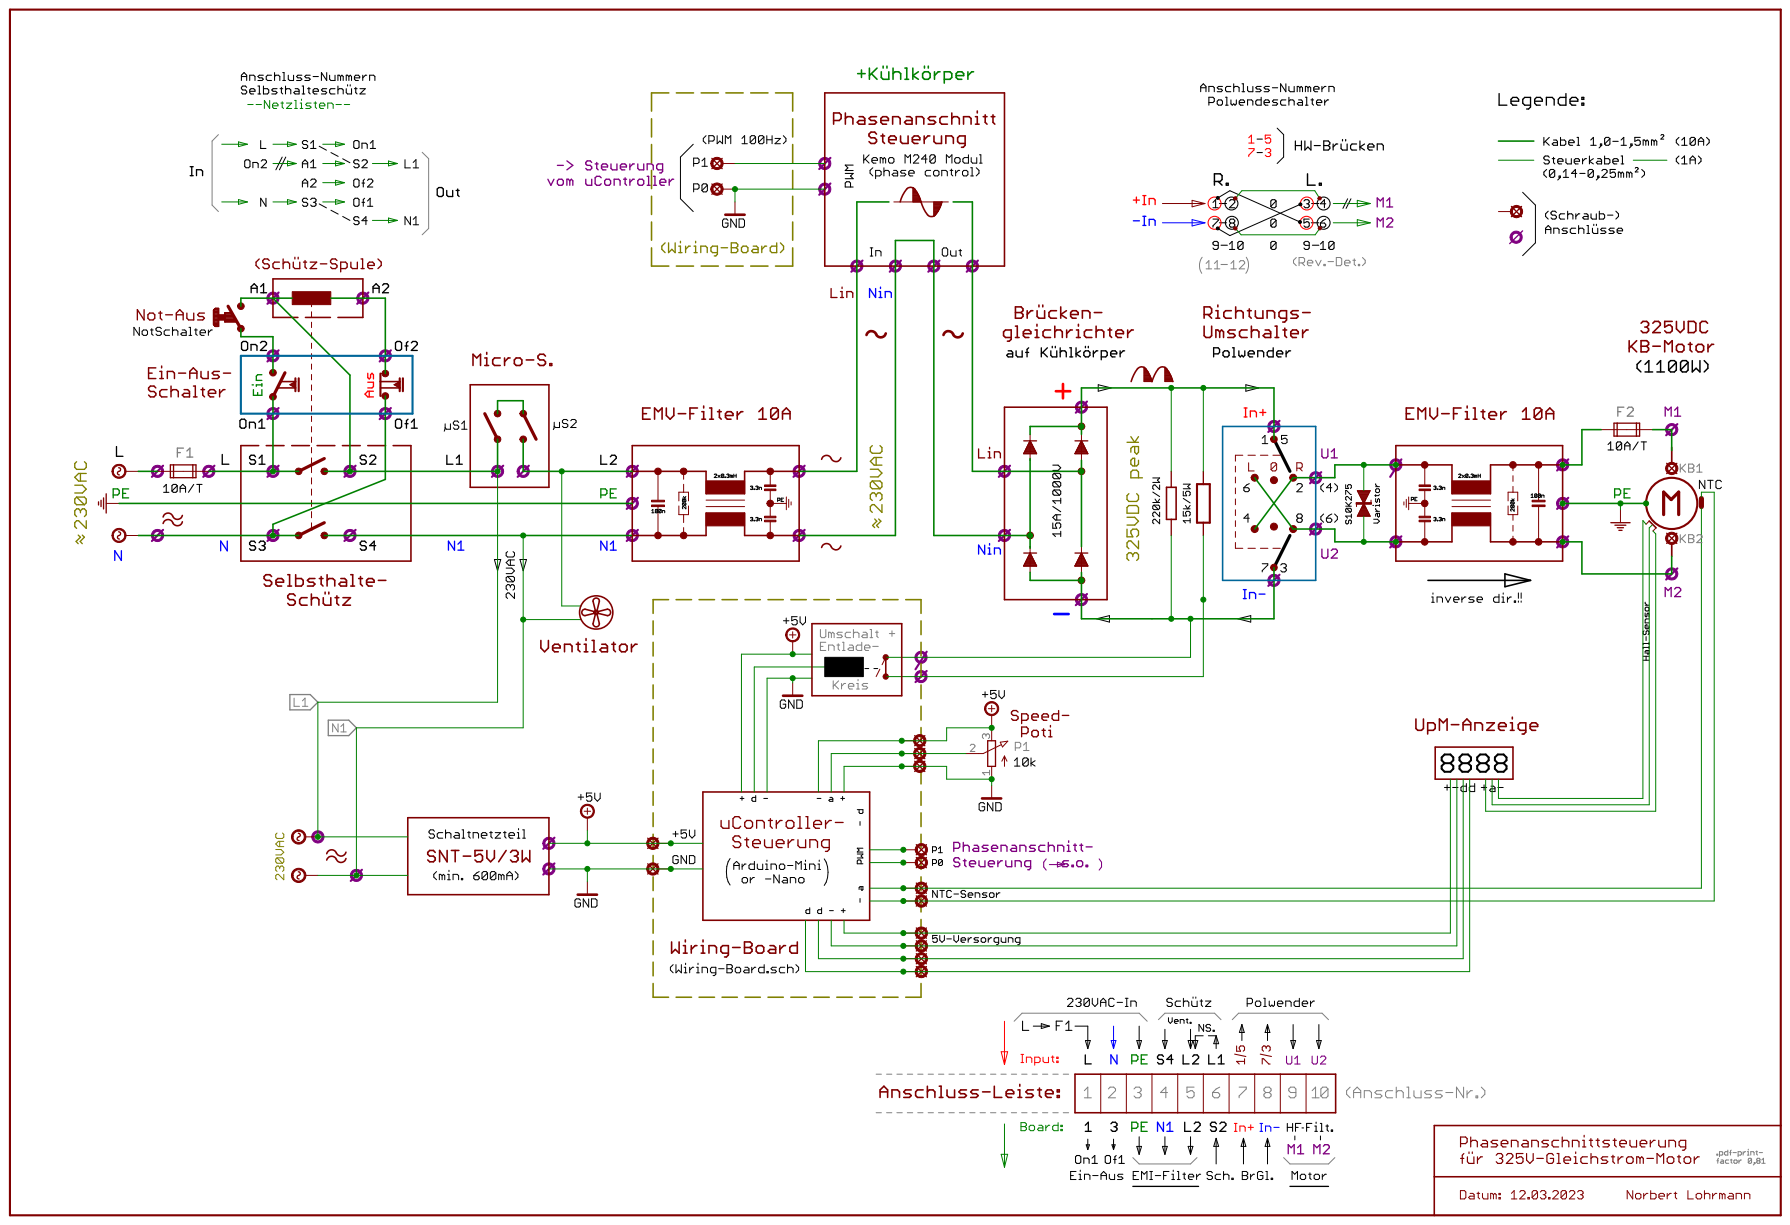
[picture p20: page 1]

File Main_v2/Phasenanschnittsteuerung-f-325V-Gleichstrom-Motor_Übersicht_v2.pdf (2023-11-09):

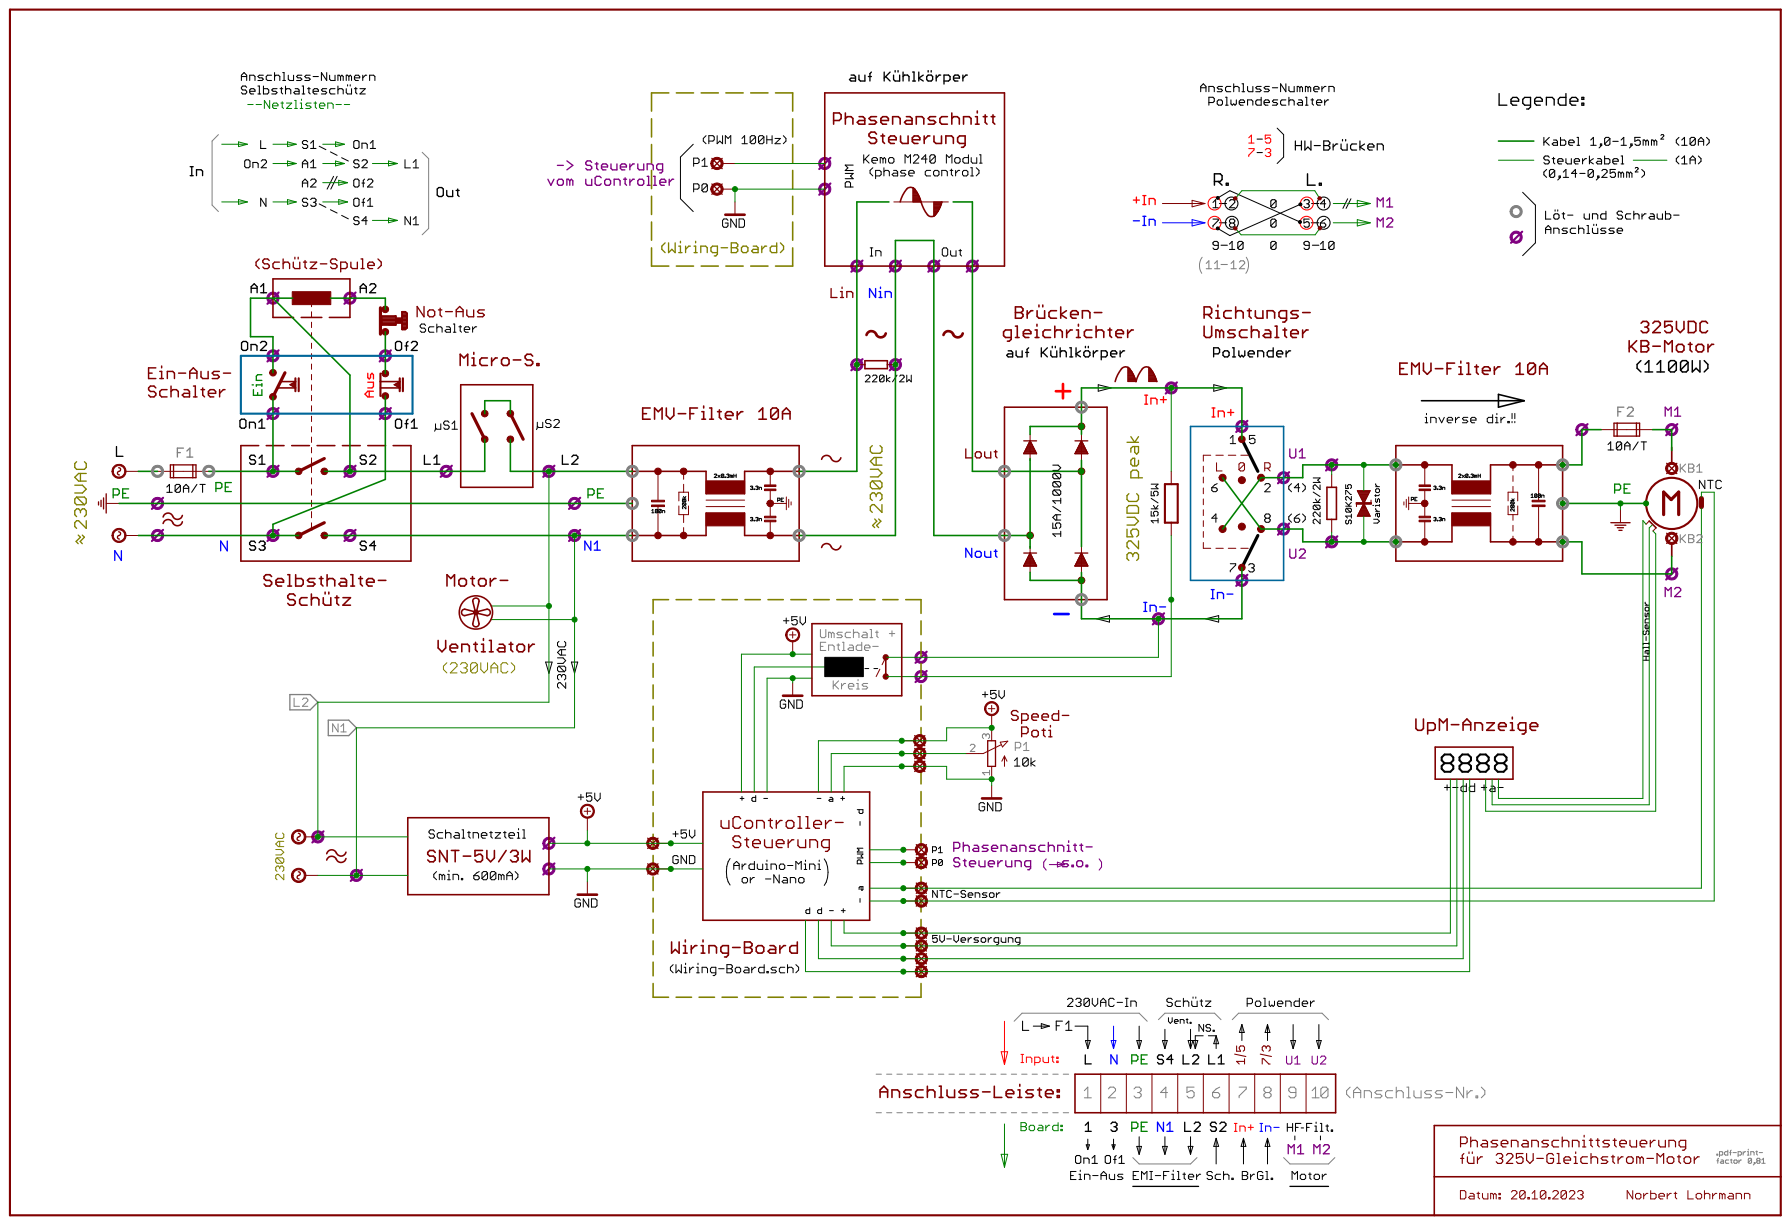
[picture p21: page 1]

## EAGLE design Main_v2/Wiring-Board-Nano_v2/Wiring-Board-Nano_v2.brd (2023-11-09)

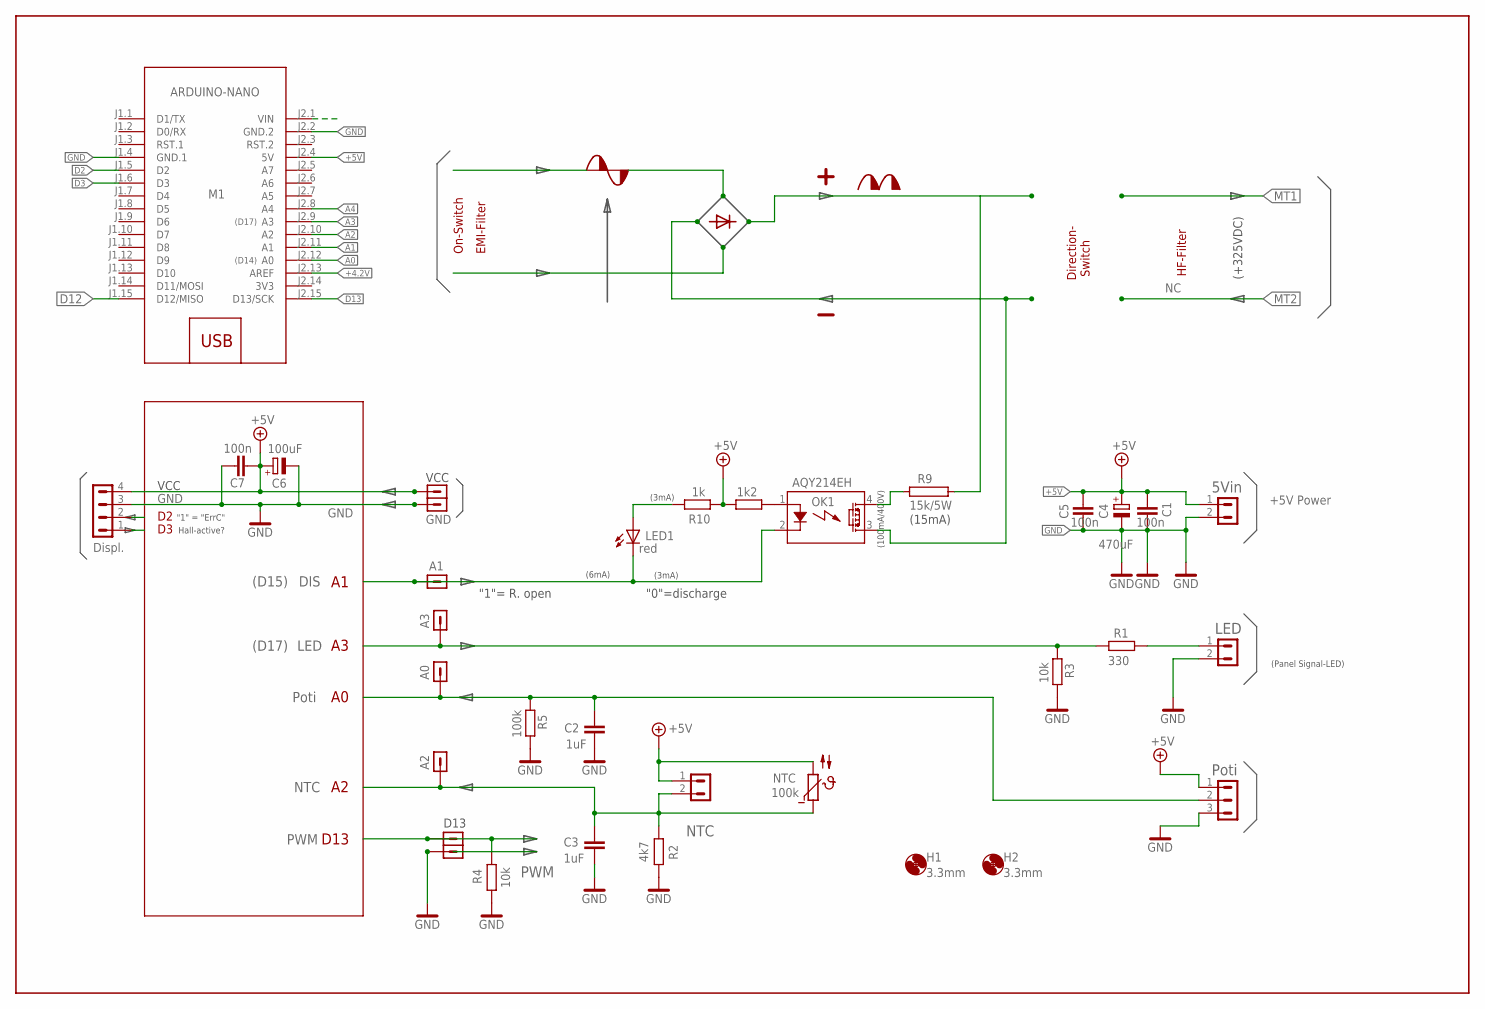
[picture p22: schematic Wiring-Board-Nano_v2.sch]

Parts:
C1, C5, C7: 100n; C0805
C2, C3: 1uF; C0805
C4: 470uF; E3,5-8
C6: 100uF; E2,5-7
H1, H2: 3.3mm; 3,3
LED1: red; CHIPLED_0805
M1: ARDUINO-NANO; ARDUINO-NANO-3.0
OK1: AQY214EH; GULLWING
R1: 330; R0805
R2: 4k7; R0805
R3, R4: 10k; R0805
R5: 100k; R0805
R9: 15k/5W; KH206-8
R10: 1k; R0805
R11: 1k2; R0805
SV1: 5Vin; MA02-1
SV2: LED; MA02-1
SV3: Poti; MA03-1
SV4: NTC; MA02-1
SV6: Displ.; MA04-1

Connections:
3V3: M1.J2.14 (3V3)
+4.2V: M1.J2.13 (AREF)
+5V: C1.1, C4.+, C5.1, C6.+, C7.1, M1.J2.4 (5V), R10.2, R11.1, SV1.1, SV3.1, SV4.1, SV6.4
A0: C2.1, M1.J2.12 (A0), R5.1, SV3.2
A1: LED1.C, M1.J2.11 (A1), OK1.2 (K)
A2: C3.1, M1.J2.10 (A2), R2.2, SV4.2
A3: M1.J2.9 (A3), R1.1, R3.1
A4: M1.J2.8 (A4)
D2: M1.J1.5 (D2), SV6.2
D3: M1.J1.6 (D3), SV6.1
D12: M1.J1.15 (D12/MISO)
D13: M1.J2.15 (D13/SCK), R4.1
GND: C1.2, C2.2, C3.2, C4.-, C5.2, C6.-, C7.2, M1.J1.4 (GND.1), M1.J2.2 (GND.2), R2.1, R3.2, R4.2, R5.2, SV1.2, SV2.2, SV3.3, SV6.3
MINUS: OK1.3 (DS2)
unnamed: OK1.1 (A), R11.2
unnamed: R1.2, SV2.1
unnamed: OK1.4 (DS1), R9.1
unnamed: LED1.A, R10.1
PLUS: R9.2

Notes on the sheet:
NTC
100k
D13
EMI-Filter
On-Switch
HF-Filter
(+325VDC)
Direction- Switch
+5V Power
(D17)
(D14)
(Panel Signal-LED)
Poti
LED
DIS
PWM
(D15)
GND
VCC
(15mA)
(100mA/400V)
(3mA)
Hall-active?
"1" = "ErrC"
"1"= R. open
(6mA)
"0"=discharge

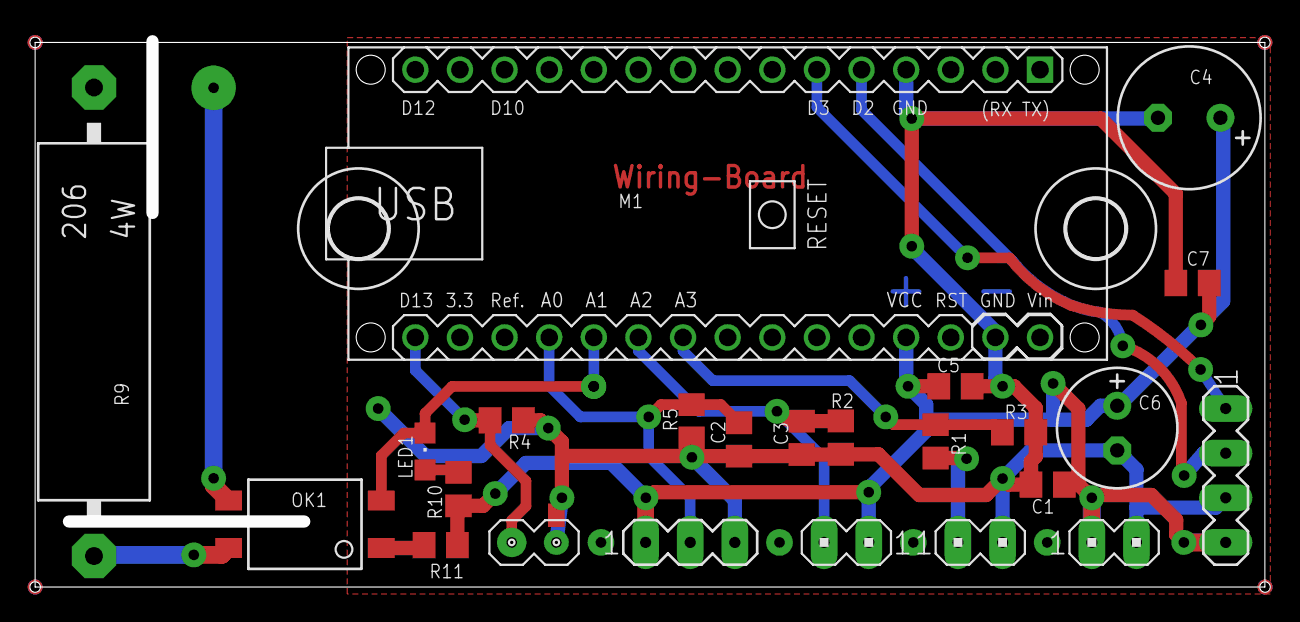
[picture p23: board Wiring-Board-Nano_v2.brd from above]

Board: 2 copper layers, 70.0 x 31.0 mm, 25 parts (0 on the bottom side), 13 nets.

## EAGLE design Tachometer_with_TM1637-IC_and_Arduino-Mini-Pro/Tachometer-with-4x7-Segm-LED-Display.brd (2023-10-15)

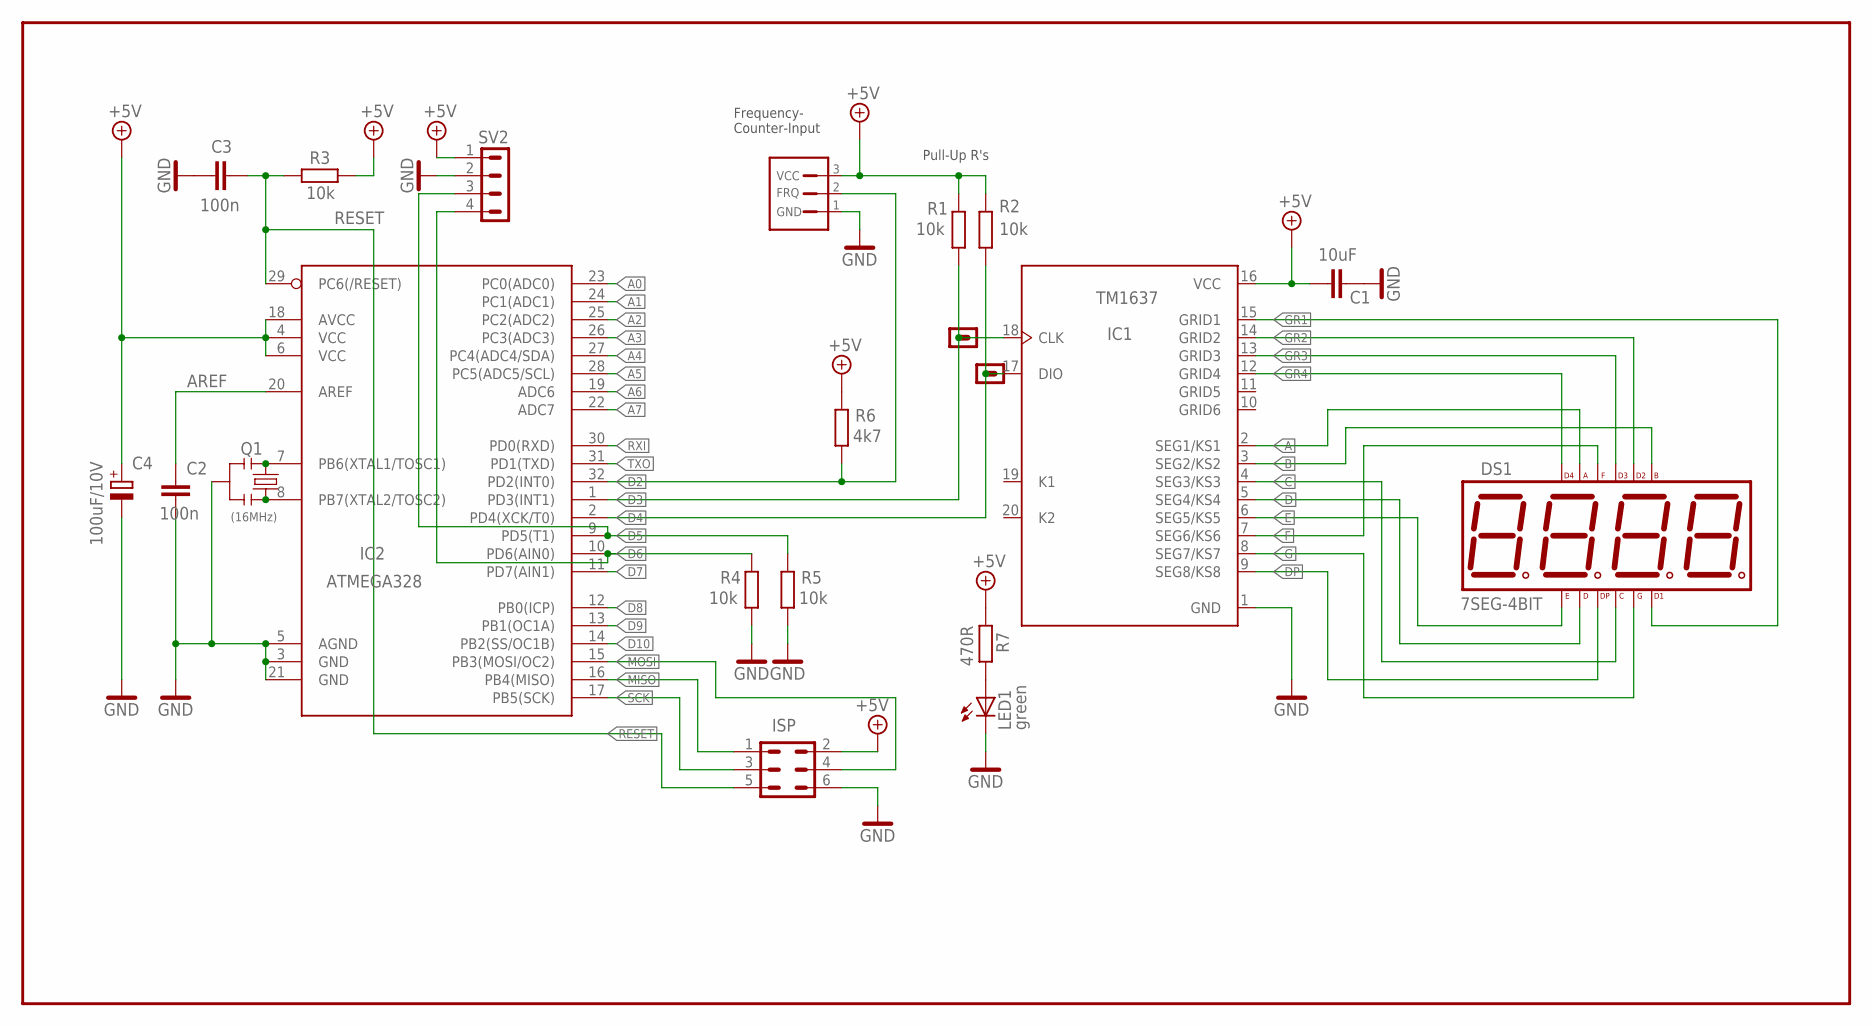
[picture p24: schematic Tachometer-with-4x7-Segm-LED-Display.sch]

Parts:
C1: 10uF; C0805
C2, C3: 100n; C0603
C4: 100uF/10V; E2,5-7
DS1: 7SEG-4BIT; 7SEG-14-4BIT
H: Hall-Ss.; 3JST-XH
IC1: TM1637; SOP-20
IC2: ATMEGA328; TQFP32-08
ISP: MA03-2
LED1: green; CHIPLED_0603
Q1: (16MHz); RESONATOR-SMD-1:1
R1, R2, R3, R4, R5: 10k; R0603
R6: 4k7; R0603
R7: 470R; R0603
SV2: MA04-10; MA04-1

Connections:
+5V: C1.1, C4.+, H.1, IC1.16 (VCC), IC2.4 (VCC), IC2.6 (VCC), IC2.18 (AVCC), ISP.2, R1.2, R2.2, R3.2, R6.2, R7.1, SV2.1
A: DS1.A, IC1.2 (SEG1/KS1)
A0: IC2.23 (PC0(ADC0))
A1: IC2.24 (PC1(ADC1))
A2: IC2.25 (PC2(ADC2))
A3: IC2.26 (PC3(ADC3))
A4: IC2.27 (PC4(ADC4/SDA))
A5: IC2.28 (PC5(ADC5/SCL))
A6: IC2.19 (ADC6)
A7: IC2.22 (ADC7)
AREF: C2.1, IC2.20 (AREF)
B: DS1.B, IC1.3 (SEG2/KS2)
C: DS1.C, IC1.4 (SEG3/KS3)
D: DS1.D, IC1.5 (SEG4/KS4)
D2: H.2, IC2.32 (PD2(INT0)), R6.1
D3: IC1.18 (CLK), IC2.1 (PD3(INT1)), R1.1
D4: IC1.17 (DIO), IC2.2 (PD4(XCK/T0)), R2.1
D5: IC2.9 (PD5(T1)), R5.2, SV2.3
D6: IC2.10 (PD6(AIN0)), R4.2, SV2.4
D7: IC2.11 (PD7(AIN1))
D8: IC2.12 (PB0(ICP))
D9: IC2.13 (PB1(OC1A))
D10: IC2.14 (PB2(SS/OC1B))
DP: DS1.DP, IC1.9 (SEG8/KS8)
E: DS1.E, IC1.6 (SEG5/KS5)
F: DS1.F, IC1.7 (SEG6/KS6)
G: DS1.G, IC1.8 (SEG7/KS7)
GND: C1.2, C2.2, C3.1, C4.-, H.3, IC1.1 (GND), IC2.3 (GND), IC2.5 (AGND), IC2.21 (GND), ISP.6, LED1.C, Q1.2, R4.1, R5.1, SV2.2
GR1: DS1.D1, IC1.15 (GRID1)
GR2: DS1.D2, IC1.14 (GRID2)
GR3: DS1.D3, IC1.13 (GRID3)
GR4: DS1.D4, IC1.12 (GRID4)
MISO: IC2.16 (PB4(MISO)), ISP.1
MOSI: IC2.15 (PB3(MOSI/OC2)), ISP.4
unnamed: LED1.A, R7.2
unnamed: IC2.8 (PB7(XTAL2/TOSC2)), Q1.3
unnamed: IC2.7 (PB6(XTAL1/TOSC1)), Q1.1
RESET: C3.2, IC2.29 (PC6(/RESET)), ISP.5, R3.1
RXI: IC2.30 (PD0(RXD))
SCK: IC2.17 (PB5(SCK)), ISP.3
TXO: IC2.31 (PD1(TXD))

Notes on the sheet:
FRQ
GND
VCC
Frequency- Counter-Input
Pull-Up R's

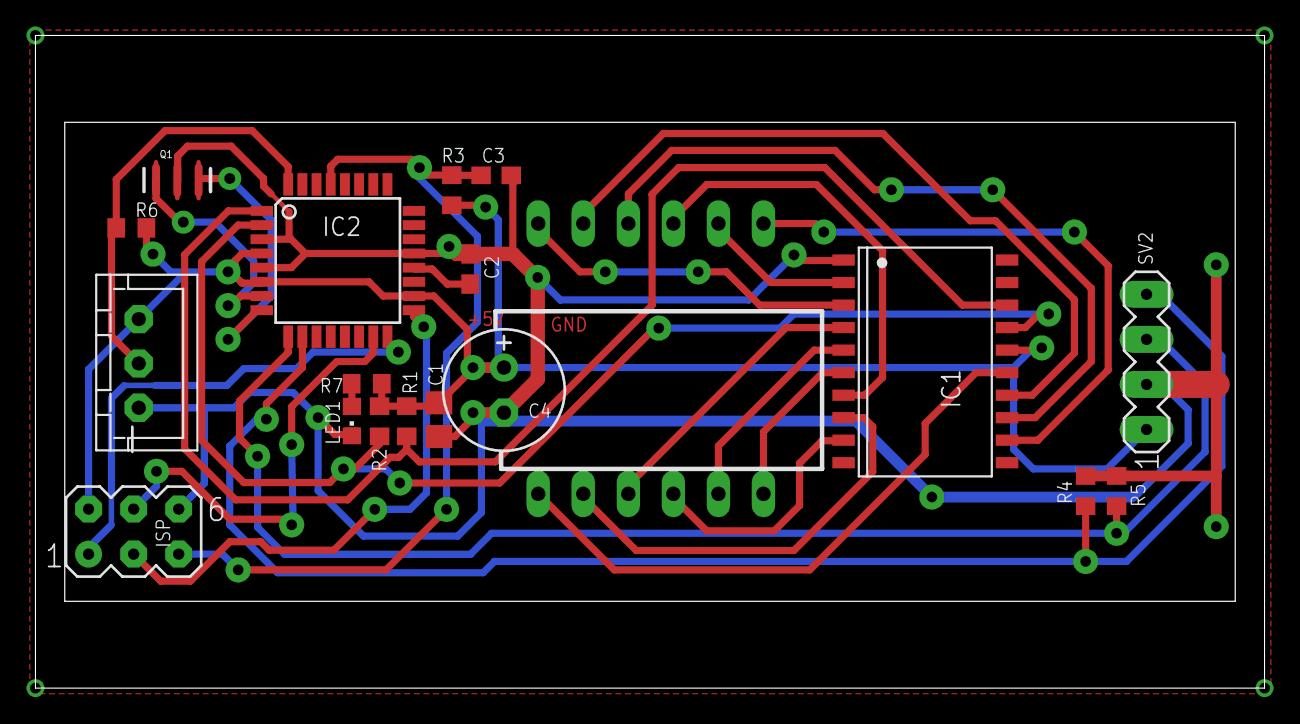
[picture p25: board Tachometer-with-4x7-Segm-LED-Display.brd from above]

Board: 2 copper layers, 69.3 x 36.8 mm, 19 parts (1 on the bottom side), 27 nets.

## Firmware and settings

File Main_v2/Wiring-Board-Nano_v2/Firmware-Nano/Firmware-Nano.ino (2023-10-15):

//Firmware for Arduino-Mini (ATMega328) - PWM-Control for Brushed *DC*-Motor 325V
/*
Main features:
- PWM-generation with a 10k-Poti + Arduino-"analogRead() from Pin-A0 to PWM-Out on Pin-D13 (with about 125Hz),
- Integrated Overcurrent-Shutdown *within* the "Kemo-240" Phase-Control-Module, if motor is overloaded or shocked,
- Integrated also a Soft-Start for motors (up to ~3600 Watt), to avoid abrupt Motor + Load-Stress (16A max. fuses),
- Overtemperature shutdown with NTC (100kOhm-Sensor/Resistor, inbuilt/inside the motor) - if temperature exceeds 80°C,
- Direction of rotation switching: only possible if incoming Tachometer-Signal on Pin-D3 is "0" (=if machine stands still)

//Arduino-Nano Pin-connections: Input or Output?
//-----------------------------
⇒ All Pins refer to the common GND (+5V Low-Voltage-Supply: "1" = 5V, "0" = 0V)
A0 ... 10k-Poti    Analog-In coming from 10k-Poti (middle-pin), grounded with 100k
A1 ... Discharge   Digital-Out (= digital Pin-D15), grounded with 10k
A2 ... NTC         Analog-In   (= digital Pin-D16), attached to GND through 4,7k resistance
A3 ... Signal-LED  Digital-Out (= digital Pin-D17), grounded with 10k
D13 .. PWM         Digital-Out to phase-control module (Kemo-240), grounded with 10k (security)
D2     "ErrC"      Digital-Out "1"=5V, to indicate Overtemperature-Signal on Tachometer (= 4x 7bit-LED-Display)
D3....."On"        Digital-In from Tachometer (Hall-Sensor), if D3="1", then A1="1". To disconnect the 15k-Discharge-Resistor R9, deactivate the Optocoupler (with D3=1).
*/

//GLOBAL VARIABLES:
int val, vals = 0;  //Input from A0: value-portion of 2^10 = 1023, correlating to the analog Poti-position (vals = val*8)
unsigned long prevPulse; //timebase for PWM (=)
int ampere = 0;     //variable for analogRead(A1) ⇐ Hall-Sensor, measuring the Motor-Current (in Volt)
int amps = 0;       //variable to average = ampere per 0.1s
float corr = 1.0;   //val-multiplier for Power-readjustment
//byte count = 0;   //counter-variable (?)
int tempC = 0;      //Input from A2: variable for analogRead(A2) (with NTC-3950) on Pin-A2 / Input of Motor-Temperature
boolean errorC = 0; //variable to indicate that motor-temperature is too high
boolean error = 0;  //variable for blinking the Signal-LED on Pin-D17 (=A3)
unsigned long previous; //timebase for blinking Signal-LED (400ms)


//////////////////////////////////////////////////////////////////////////
void setup() {
  //Serial.begin(115200); //initializing the serial-COM - not needed here.

//Input-Pins: A0, A2 and D3 don't need initialization - this Input-Pins (and also some Output-Pins) here are grounded externally (10k and 100k), and additionally...
//...Arduino sets all "A"- and "D"-Pins on start or reset to floating-INPUTS. Only Output-A1 is inactivated to "+5V", because its goal is to discharge when m. in idle-mode.
//Input-D3, coming from Tacho: if Hall-Detector sends impulses (=machine running), D3=1 , else if m. stopped, D3=0). Initially machine stands still, so on begin D3 = 0.

//Output-Pins: A1, A3, D13 and D2 (same order as in the schematic):
  pinMode(A1, OUTPUT);  digitalWrite(A1, LOW);  //set Pin-A1 as Output for the discharge-control, to discharge charged capacitors while machine is idle, so initially LOW=connected.
  pinMode(A3, OUTPUT);  digitalWrite(A3, HIGH); //set Pin-A3 (D17) as Output for Signal-LED ⇒ Signal-LED shining if "machine ready" (if "On/Off"-Switch is "On") at setup() time.
  pinMode(13, OUTPUT);  digitalWrite(13, LOW);  //set Pin-D13 as Output for PWM-Control - with initial PWM-state "off" (for security).
  pinMode(2, OUTPUT);   digitalWrite(2, LOW);   //set Pin-D2 as Output for "ErrC"-Signal to Tachometer/LED-Display => if D2=1, Tach. displays "ErrC" and machine goes into stand-by.
}
//////////////////////////////////////////////////////////////////////////

//Switch-On/Off A1 = 0 (⇒ 230V main-line-Switch from 30A-Relay)

///////////////////////////////////////////////////////////////////////////////////////////////
//***************************************** Main-Loop *****************************************
void loop() {
//PWM-width: Input from 10k-Poti (analog-voltage on Pin-A0) ⇒ translated as PWM output on Pin-D13 (=PB5):
  val = analogRead(A0); //Voltage on Input-pin A0 (from 10k Poti middle-pin), "val" variable stores values betw. 0-1023 corresponding to actual poti-position.
  //Skip "mapping" analog-values (usually from 0 to 255), using the output-values 0-1023 directly from analogRead(0-1023 bits to µs) as PWM-timing-values:
  //Desired PWM-width: Input from voltage on Pin-A0 (10k-Poti), translated as PWM output on Pin-D13 in microseconds (µs):
  vals = map (val, 0,1023, 0,8160);       //"vals" = spreaded val*8 ⇒ greater accuracy for the PWM-timing ⇒ no need to use high PWM-frequencies (Kemo-240 PWM-Module: 10...10kHz),
  //add upper and lower "dead-band":      //adding security "dead-bands", to avoid glitches on both endpoints of the 10k-Poti, caused by evtl. not so stable +5V Power-Input, etc.
  if (vals < 96) { vals = 0; }            //⇒ Resulting bandwidth = "0" to 8160 µs, where "0" = 104 (= 8256 - (1023 *8)) = "deadband"-difference for "0"...
  if (vals > 8000) { vals = 8000; }       //...to be absolutely sure that also upper values (peaks + glitches over 5V?) don't not overflow the upper value (=8256).
  if (!errorC) {                          //If motor-temperature isn't too heigh [see "analogRead(A2)" + "tempC" below] - then go PWM:
    //PWM-Output on Pin-D13 using "Port-manipulation with BitMath": see https://wolles-elektronikkiste.de/en/logical-operations-and-port-manipulation
    if (micros() - prevPulse >= 8256 - (vals*0.7)) { //0.7 = 70% bec. Kemo-240 module uses only ~70% of PWM-bandwidth, so "max."-value is (vals*0.7) ⇒ upper deadband,
      PORTB |= (1 << PB5); }              //this sets output on D13 = HIGH, (Pin-D13 = PB5), "OR"ing PORTB with PB5 (=Pin-D13) sets D13 HIGH, but keeps all others unchanged,
    if (micros() - prevPulse >= 8160) {   //8256 = time in µs for duration of a complete PWM-cycle + 96µs (upper-)deadband,
      PORTB &= ~(1 << PB5);               //this sets output on D13 = LOW, (Pin-D13 = PB5), "AND"ing + Inverting PORTB with PB5 sets D13 LOW, keeping all others unchanged.
      prevPulse = micros();               //actualize "prevPulse"-variable each time "micros()" surpasses pwm-frequency (max. pulse-length-time = 8256 us ≙ ~120Hz).
    }
  }

//Discharge-Resistance: Pin-A1 (D15): if LOW, disconnects 15k/5W-Resistor if machine is in action, while connecting it if machine is in idle-state (discharging).
//"machine running/stopped" is dependent from incoming Tachometer-Signal on Input-D3 !! (see ⇒ modified Arduino-Mini-Tachometer ⇒ "Tachometer-with-4x7-Segm-LED-Display.sch")
//---------------------
  if (digitalRead(3) == LOW) { digitalWrite(A1, LOW); }  //if incoming  LOW on Pin-D3 (=machine STOPPED), set A1 to LOW, to activate Discharge-circuit ⇒ R9 connected
  else { digitalWrite(A1, HIGH); }                       //if incoming HIGH on Pin-D3 (=machine RUNNING), set A1 to HIGH, disconnecting R9 to protect it against overtemperature.


//Pin-A2 Analog-Input from NTC-Sensor:
//Shutdown if Motor-Temperature gets higher than 80°C: (NTC-3950 on Pin-A2 - "NTC" = NegativeTemperatureCoefficient Temp.-Sensor)
  tempC = analogRead(A2);         //Read the analog-voltage on Pin-A2 Input (NTC 100kOhm, see values from Thermistor-Table)
//Calculation for NTC min.Value @ 80°C:  (NTC = Negative Temperature Coefficient!, see "NTC-Widerstands-Schaltung.png" !)
//-------------------------------------
//25°C ⇒ 100k ⇒ OK     ⇒  x1 ≈ 0,22 V ... @ 25°C (from 5V total)   ⇒ calculation: "Widerstands-Teiler bei gegebenen Voltzahlen !.htm"
//80°C ⇒  12k ⇒ NOK    ⇒  x2 ≈ 3,59 V ... @ 80°C (min. value!)     ⇒  " " " "
//5,0 V ... 1023 bits   ; Y1 = 1023 * 0,22 / 5 = ≈ 45 bits @ 25°C
//3,59V ...    x bits   ; y2 = 1023 * 3,59 / 5 = ≈735 bits @ 80°C (=max. value)
//Input Pin-A2:
  if (tempC >= 735) {             //100k-NTC at 80°C ⇒ ~12kOhm, so if 4,7k (=lower-R) + 12k NTC (upper-R = NTC !), then tempC goes up over >3,59V and "errorC" becomes valid,
    errorC = 1;                   //if above 80°C, set variable to "1" and
    while(errorC) {               //if this condition is true ⇒ then HALT! and rest here within while-loop, until reset...
      digitalWrite(13, LOW);      //disable PWM-Out (set duty-cycle on Pin-D13 to "0" = PWM-output on Pin-D13 "LOW" = machine halt)
      digitalWrite(2, HIGH);      //Pin-D2 LOW-signal on output of Arduino-Nano (to show "ErrC" on LED-Display, forwarded to input on L.D.-Arduino-Mini-Pro, input Pin-D5)
      if (millis() - previous >= 400) { //Signal-LED:
        previous = millis();      //actualize "previous" variable each 400ms,
        if (error == 0) { error = 1; } //invert "error" (helper variable to blink Signal-LED)
        else error = 0;                // " " " "
        digitalWrite(A3, error);  //blinking Signal-LED on A3 = Pin-D17 - if temperature is too high (NTC lower than 12k if >80°C)
      }
    }
  } else { errorC = 0; }          //if temperature is normal (< 80°C)

}
//************************************* End of Main-Loop **************************************
///////////////////////////////////////////////////////////////////////////////////////////////


/*~~~~~~~~~~~~~~~~~~~~~~~~~~~~~~~~~~~~~~~~~~~~~~~~~~~~~~~~~~~~~~~~~~~~~~~~~~~~~~~~~~~~~~~~~~~~~~~~~~~
/////////////////////////////////////////////////////////////////////////////////////////////////////
Flashing the chip (atmega328) directly = without bootloader from "cmd" command-line: starting faster!
avrdude.exe -v -V -p m328p -c usbasp -e -D -U flash:w:Firmware-Nano.ino.hex:i

Fuses:                                                                             (0xfd: Brown-out-level @VCC = 2,7V)
avrdude.exe -v -V -p m328p -c usbasp -U lfuse:w:0xe2:m -U hfuse:w:0xd9:m -U efuse:w:0xfd:m      orig: E:FD, H:DA, L:FF
/////////////////////////////////////////////////////////////////////////////////////////////////////

⇒ Result: "avrdude: writing flash (2462 bytes)"
~~~~~~~~~~~~~~~~~~~~~~~~~~~~~~~~~~~~~~~~~~~~~~~~~~~~~~~~~~~~~~~~~~~~~~~~~~~~~~~~~~~~~~~~~~~~~~~~~~~~~
*/

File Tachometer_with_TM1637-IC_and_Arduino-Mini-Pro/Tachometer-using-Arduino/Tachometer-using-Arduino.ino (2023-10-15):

/*
Arduino-based Tachometer using an Arduino-Mini-Pro with 4x7-LED-Display (incl. TM1637 control-IC)
------------------------
!!! Best +working example with Timer-1: https://quartzcomponents.com/blogs/electronics-projects/arduino-based-tachometer-rpm-meter-using-ir-sensor
Instructions to set Timers ⇒ https://wolles-elektronikkiste.de/timer-und-pwm-teil-2-16-bit-timer1
Calculate Timer Prescaler-values ⇒ http://evolutec.publicmsg.de/index.php?menu=software&content=prescalertools
Adapted on 06.09.2023 (nl):

Tachometer displays 4 states:
-----------------------------
1. Displays rpm-value (1-9999 rpm)
2. Displays "----" if machine is idle
3. Displays "ErrC" if Temperature-Sensor-Signal on Pin-D2 (input) is HIGH
4. Displays "HHHH" if rpm overflows the capability of the 4x7-digit LED-Display (>9999)

Arduino-Mini-Pro Pin-connections:
---------------------------------
D2 ... Frequency   Digital-In  from Hall-Sensor (! Important: with external 4,7k Pull-Up Resistance for Hall-S. with Open-Collector - to avoid "floating" signal!)
D3 ... CLK         Digital-Out (to TM1637-IC - I²C-communication, Pin-18)
D4 ... DIO         Digital-Out (to TM1637-IC - I²C-communication, Pin-17)
D5 ... "ErrC"      Digital-In  ("1" = Signal for Overtemperature, computed from external uContoller, there Pin-D2)
D6 ... "On"        Digital-Out ("1" = Signal from Hall-Sensor = "machine-active", feedback to external uContoller, there Pin-D3)
*/

//4x 7-Segment LED-Display with TM1637-IC:
#include <SevenSegmentTM1637.h>
const byte CLK = 3;     //define CLK pin (any digital pin) //Connection from Arduino-D3 to Display-Driver-IC TM1637
const byte DIO = 4;     //define DIO pin (any digital pin) //Connection from Arduino-D4 to Display-Driver-IC TM1637

SevenSegmentTM1637  display(CLK, DIO); //initialize the 4x 7-segm-LED-Display (0,56" height) //CLK = 4; DIO = 5;

unsigned long preset;	//timing-base for 16bit timer-1
float rpmflt;					//total time counting-up
unsigned int rpm;			//revolutions per minute
boolean tooslow = 1;	//if no signal is incoming, timer doesn't count-up

void setup() {
	Serial.begin(9600);

//Set Input-Pin register (Timer1 "INT0" on Port-Pin PD2 = Pin-D2):
	TCCR1A = 0;		//(re)set the 16bit Timer/Counter1 Control Register "TCCR1A" to 0 (Waveform = WGR10 to R/W ; WGR10 = Waveform Generation Mode, set bit identifier to 0)
	TCCR1B = 0;		//reset TCCR1B (Timer/Counter1 Control Register 1B )
	TCCR1B |= (1 << CS12);		//set Timer-1 mode CS12 (bit-2) as 256 prescaler (nl: set variable "preset" = 16MHz / 256 = 62500, see "rpmflt"-value below)
	TIMSK1 |= (1 << TOIE1);		//Enable timer1 overflow *interrupt* (TOIE1) by setting global interrupt *enable* bit in SREG
	pinMode(2, INPUT_PULLUP);	//Pin-D2 as digital Hall-Signal input. Grounded per hardware, so input isn't floating if no signal is incoming!
	pinMode(6, OUTPUT); digitalWrite(6, LOW); //set Pin-D6 as output, LOW on begin (supposing that on begin machine is in idle-mode, standing still)
	//Input-Pins don't need initialization

attachInterrupt(0, RevPM, FALLING); //attachs the function "RevPM", below

//LED-Display:
	display.begin();						//initializes the LED-Display
	display.setBacklight(100);	//sets the brightness to 100%
}

void RevPM() { //
	preset = TCNT1;	//timer1 Clock Select Bits / Prescaler (= prescaler, set to 65200 ms, see calculation below)
	TCNT1 = 0;			//"TCNT1" = Timer1 Counter Register counting-up from "0" (see https://forum.arduino.cc/t/ch-9-timer-counter-module-of-atmega328p-mcu/662590)	
	tooslow = 0;		//reset flag for normal use
}

ISR(TIMER1_OVF_vect) {	//set Timer1 ISR (InterruptServiceRoutine) to "Timer Overflow" (normal mode)
	tooslow = 1;					//if no-signal is incoming on Pin-D2, Timer1 doesn't count-up...
}

void loop() {

	if (tooslow == 1) {
		Serial.println("---");
		display.clear(); display.setCursor(0,0); //clear the Display and set the cursor to the 4th position (left)
		display.print("----");
		digitalWrite(6, LOW);  //Signal to external uController to indicate that machine is standing still (no Halls-Sensor-Signal coming-in)
	} else {
//	rpmflt = 120 / (rpmtime / 31250.00);	//nl: why? ⇒ 31250 = 62500/2 (in float units), using the preset-*base* of 16MHz/256 = 62500 Hz
		rpmflt =  (30 * 31250.00) / preset;		//15 instead of 60 seconds/minute - resp. 30 of 120, bec. of 4 Magnets on machine-axle! (15=60/4) - for rpm
		rpm = (round(rpmflt)); 								//rounding rpmflt = rpm without decimals (to use it as int)
		if (rpm >=9999) { rpm = 9999; }				//limit rpm to 9999 (don't overflow)
		digitalWrite(6, HIGH); //Signal to external uController to indicate that machine is running (= Hall-Sensor-Siganl coming-in)
		Serial.println(rpm);

		//Forward RpM to LED-Display (once per ½-second):
		display.clear(); //clear the display and show the actual RpM on LED-Display:
		if (rpm <10)									{ display.setCursor(0,3); display.print(rpm); } //right side
		if ((rpm <100) && (rpm >10))	{ display.setCursor(0,2); display.print(rpm); } //m-r. ""
		if ((rpm <1000) && (rpm >100)){ display.setCursor(0,1); display.print(rpm); } //m-l. ""
		if	 (rpm >=1000)							{ display.setCursor(0,0); display.print(rpm); } //left side
		if (rpm >=9999)								{ display.setCursor(0,0); display.print("HHHH"); } //if it overflows, don't go rambling, display "rpm too high"
		if (digitalRead(5) == HIGH)		{ display.setCursor(0,0); display.print("ErrC"); } //display overheat-warning if Input-Pin D5 is HIGH
	}

	delay(500); //renew display each ½-second

} //end of loop

/*~~~~~~~~~~~~~~~~~~~~~~~~~~~~~~~~~~~~~~~~~~~~~~~~~~~~~~~~~~~~~~~~~~~~~~~~~~~~~~~~~~~~
//////////////////////////////////////////////////////////////////////////////////////
Flashing the chip (atmega328) directly = without bootloader (from "cmd" command-line):
avrdude.exe -v -V -p m328p -c usbasp -e -D -U flash:w:Tachometer-using-Arduino.ino.hex.hex:i

Fuses:                                                                             (0xfd: Brown-out-level @VCC = 2,7V)
avrdude.exe -v -V -p m328p -c usbasp -U lfuse:w:0xe2:m -U hfuse:w:0xd9:m -U efuse:w:0xfd:m      orig: E:FD, H:DA, L:FF

//////////////////////////////////////////////////////////////////////////////////////
~~~~~~~~~~~~~~~~~~~~~~~~~~~~~~~~~~~~~~~~~~~~~~~~~~~~~~~~~~~~~~~~~~~~~~~~~~~~~~~~~~~~~~
*/

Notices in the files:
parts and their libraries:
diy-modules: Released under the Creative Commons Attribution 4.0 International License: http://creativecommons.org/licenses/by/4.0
